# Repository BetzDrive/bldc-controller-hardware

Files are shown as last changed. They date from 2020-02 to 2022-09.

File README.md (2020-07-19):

# Betz Drive - A BLDC Controller

This board is designed for low-speed, high torque motor applications that require
highly precise positional and torque commands.

## Features

 * Chainable Initialization. Input/output connectors and 'disco-bus' pins provide
 dynamic initialization, allowing for easy replacement of any board (no hard coded ids).
 
 * High Precision Current Readings
 
 * 12-bit Precision Positional Readings [AS5047U-HTSM](https://ams.com/documents/20143/36005/AS5047U_DS000637_1-00.pdf)
 
 * Thermal Sensitivity
 
 * Optional 20-pin header with 9 GPIO pins, I2C, 3.3V rail, and ground for add-on functionality!
 
## Renderings

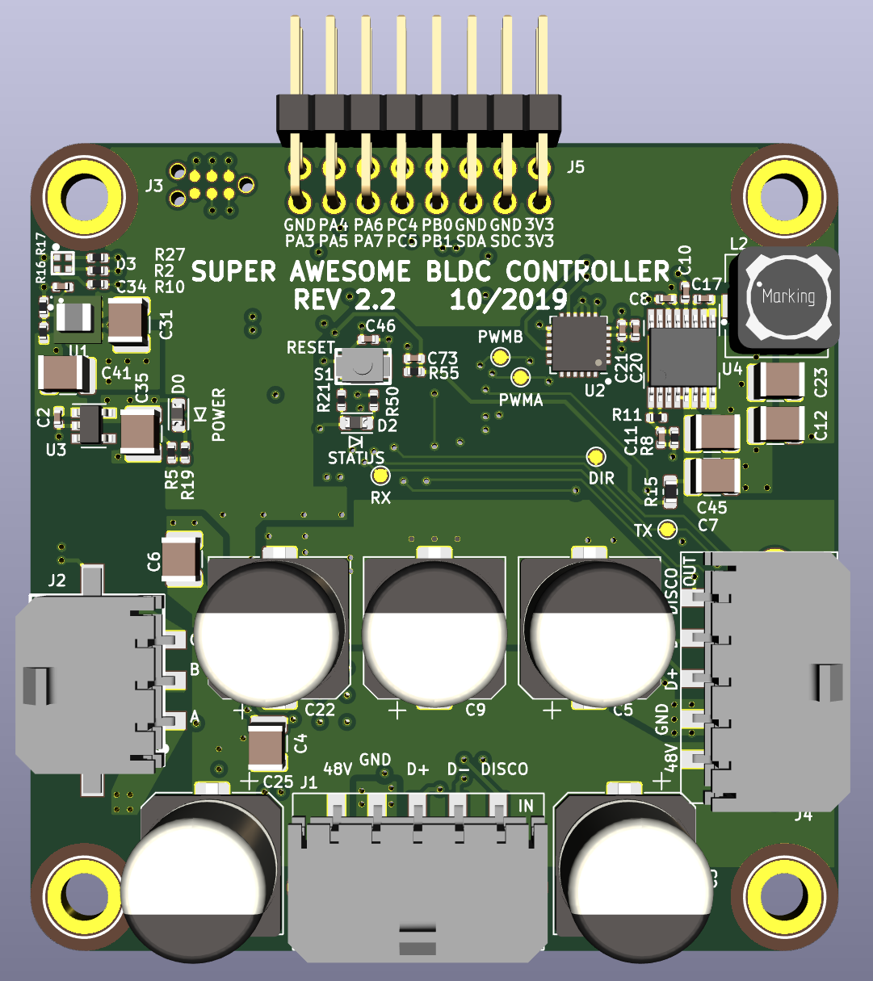
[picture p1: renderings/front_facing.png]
3D Front

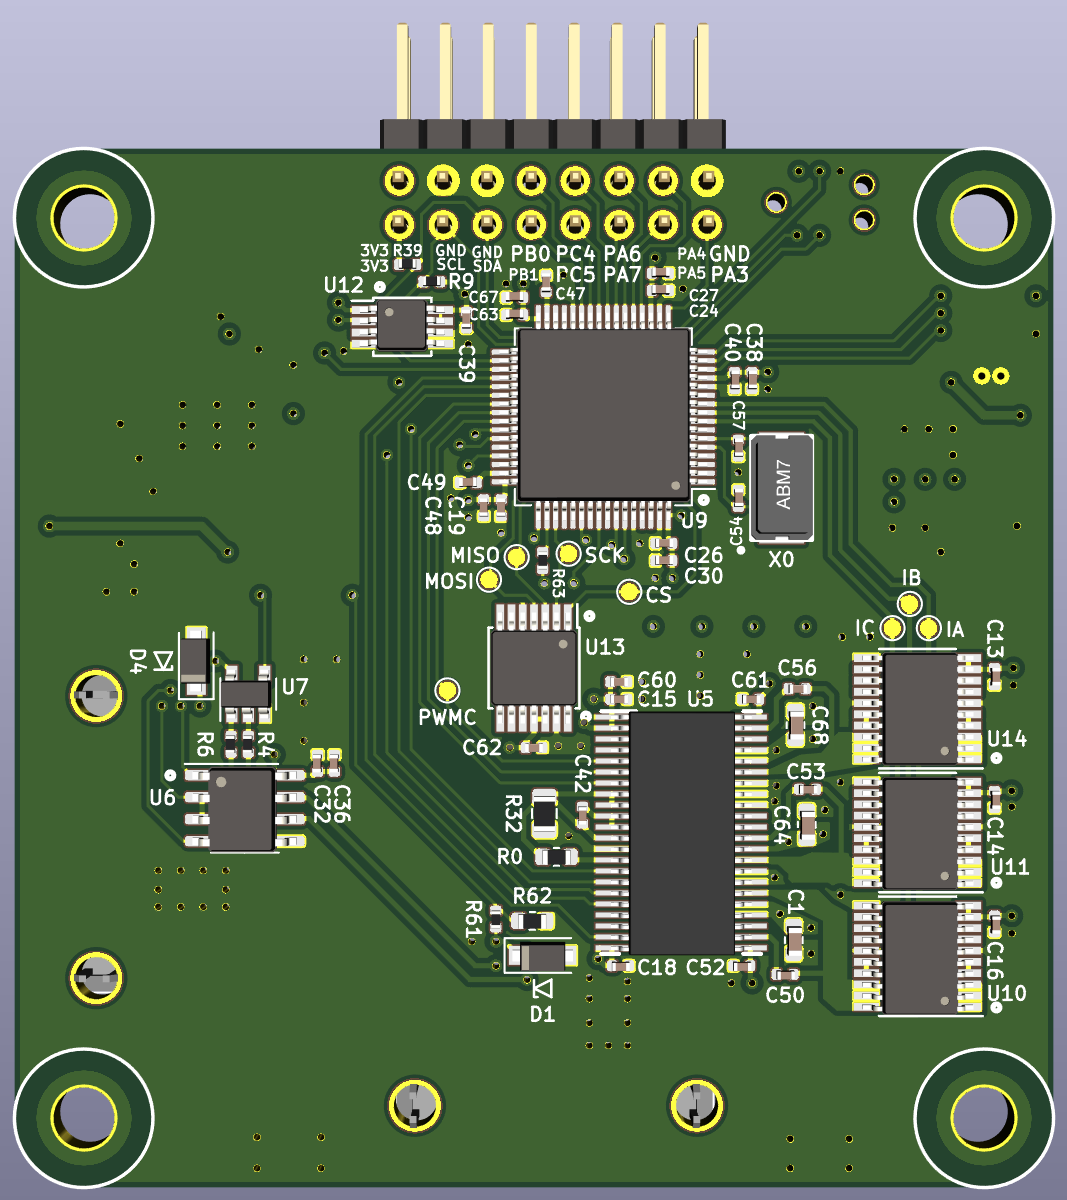
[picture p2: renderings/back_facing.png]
3D Back


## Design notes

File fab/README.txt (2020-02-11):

PCB fabrication notes
====
 * 4 layers
 * green soldermask, white silkscreen
 * rectangular, 60mm x 60mm
 * 1.6mm finished thickness
 * minimum via drill 15mil
 * minimum trace/space 7mil

Assembly notes:
====
 * double-sided SMT, heavy parts on top side
 * two connectors with through-hole mounting tabs
 * please ignore all parts with "Do Not Populate" (DNP) part numbers

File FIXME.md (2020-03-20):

 * bring an extra UART TX pin to a header for printf() debugging

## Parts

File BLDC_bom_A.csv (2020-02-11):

Component | Quantity Per PCB | References | Value | Footprint | Tolerance | MFN | MPN | D1N | D1PN | Maximum Voltage | Maximum Power
1 | 3 | C1 C64 C68 | 100n | C_0603_1608Metric | 10% | Samsung | CL10B104KC8NNNC | Digikey | 1276-6807-1-ND | 100.0V
2 | 19 | C13 C14 C16 C19 C21 C24 C26 C32 C39 C40 C42 C46 C50 C53 C56 C61 C62 C63 C73 | 100n | C_0402_1005Metric | 10% | Samsung | CL05A104KA5NNNC | Digikey | 1276-1043-1-ND | 25.0V
3 | 5 | C3 C5 C9 C22 C25 | 100u | CP_Elec_10x10 | 20% | Panasonic | EEE-1JA101P | Digikey | PCE3942CT-ND | 63.0V
4 | 2 | C54 C57 | 16p | C_0402_1005Metric | 5% | Murata | GJM1555C1H160GB01D | Digikey | 490-8081-1-ND | 50.0V
5 | 12 | C2 C15 C18 C20 C27 C30 C36 C38 C48 C52 C60 C67 | 1u | C_0402_1005Metric | 10% | Murata | GRM155R61E105KA12D | Digikey | 490-10017-1-ND | 25.0V
6 | 5 | C12 C23 C31 C35 C41 | 22u | C_1210_3225Metric | 10% | Samsung | CL32A226KAJNNNE | Digikey | 1276-1101-1-ND | 25V
7 | 4 | C8 C10 C47 C49 | 2u2 | C_0402_1005Metric | 10% | Murata | GRM155R61E225KE11D | Digikey | 490-12703-1-ND | 25.0V
8 | 1 | C17 | 470n | C_0402_1005Metric | 10% | Samsung | CL05A474KP5NNNC | Digikey | 1276-1173-1-ND | 10.0V
9 | 1 | C34 | 4n7 | C_0402_1005Metric | 10% | Yageo | CC0402KRX7R8BB472 | Digikey | 311-1039-1-ND | 25V
10 | 4 | C4 C6 C7 C45 | 4u7 | C_1210_3225Metric | 10% | TDK | C3225X7S2A475K200AB | Digikey | 445-6042-1-ND | 100V
11 | 1 | C11 | 82p | C_0402_1005Metric | 10% | AVX Corporation | 04025A820FAT2A | Digikey | 478-10115-1-ND | 50V
12 | 2 | D0 D2 | LTST-C190GKT | D_0603_1608Metric |  | Lite-On | LTST-C190GKT | Digikey | 160-1183-1-ND
13 | 2 | D1 D4 | SMF3.3 | D_SOD-123F |  | Littelfuse | SMF3.3 | Digikey | F7701CT-ND
14 | 1 | D3 | SMLP34RGB | rhom-SMLP34RGB-fp |  | Rohm | SMLP34RGB2W3 | Digikey | SMLP34RGB2W3CT-ND
15 | 2 | J1 J4 | 43650-0510 | molex-436500511 |  | Molex | 436500510 | Digikey | WM1888CT-ND
16 | 1 | J2 | 436500313 | molex-microfit-3-pkg |  | Molex | 436500313 | Digikey | WM1896CT-ND
17 | 1 | J5 | BONUS | PinHeader_2x08_P2.54mm_Horizontal |  | DNP | DNP | DNP | DNP
18 | 1 (DNF) | J3 | DNP | TC2030-MCP-NL-pkg |  | DNP | DNP | DNP | DNP
19 | 1 | L2 | 100u | L_7.3x7.3_H4.5 | 20% | Wurth | 744777920 | Digikey | 732-1199
20 | 6 | R2 R5 R10 R19 R27 R50 | 150R | R_0402_1005Metric | 1% | Panasonic | ERJ-2RKF1500X | Digikey | P150LCT-ND |  | 0.0625W
21 | 1 | R17 | 180k | R_0402_1005Metric | 1% | Yageo | RC0402FR-07180KL | Digikey | 311-180KLRCT-ND |  | 0.0625W
22 | 1 | R8 | 1M | R_0402_1005Metric | 1% | Yageo | RC0402FR-071ML | Digikey | 311-1.00MLRCT-ND |  | 0.0625W
23 | 1 | R32 | 1R | R_0805_2012Metric | 1% | Panasonic | ERJ-6DQF1R0V | Digikey | P19268CT-ND |  | 0.333W
24 | 6 | R9 R21 R39 R55 R61 R63 | 2k21 | R_0402_1005Metric | 1% | Panasonic | ERJ-2RKF2211X | Digikey | P2.21KLCT-ND |  | 0.0625W
25 | 3 | R0 R15 R62 | 49k9 | R_0603_1608Metric | 1% | Panasonic | ERJ-3EKF4992V | Digikey | P49.9KHCT-ND |  | 0.0625W
26 | 2 | R4 R6 | 56R2 | R_0402_1005Metric | 1% | Yageo | RC0402FR-0756R2L | Digikey | 311-56.2LRCT-ND |  | 0.0625W
27 | 1 | R16 | 681k | R_0402_1005Metric | 1% | Yageo | RC0402FR-07681KL | Digikey | YAG3212CT-ND |  | 0.0625W
28 | 1 | R11 | 91k | R_0402_1005Metric | 1% | Yageo | RC0402FR-0791KL | Digikey | 311-91.0KLRCT-ND |  | 0.0625W
29 | 1 | S1 | B3U-1000P | SW_B3U-1000P |  | Omron | B3U-1000P | Digikey | SW1020CT-ND
30 | 1 | U13 | AS5047U | TSSOP-14_4.4x5mm_P0.65mm |  | AMS | AS5047U-HTSM | Mouser | 985-AS5047U-HTSM
31 | 1 | U5 | DRV8312 | HTSSOP-44 |  | TI | DRV8312DDWR | Digikey | 296-29649-1-ND
32 | 1 | U2 | IIS328DQ | QFN-24-1EP_4x4mm_P0.5mm_EP2.6x2.6mm |  | ST | IIS328DQTR | Digikey | 497-15701-1-ND
33 | 3 | U10 U11 U14 | INA253 | TSSOP-20_4.4x6.5mm_P0.65mm |  | TI | INA253A2IPW | Digikey | 296-53071-ND
34 | 1 | U6 | ISL32458E | SOIC-8_3.9x4.9mm_P1.27mm |  | Renesas | ISL32458EIBZ-T7A | Digikey | ISL32458EIBZ-T7ACT-ND
35 | 1 | U4 | LM46000 | PWP0016G |  | TI | LM46000PWPR | Digikey | 296-40222-1-ND
36 | 1 | U1 | LMZ21700SIL | SIL0008E |  | TI | LMZ21700SILR | Digikey | 296-44325-1-ND
37 | 1 | U12 | MCP9808 | MSOP-8_3x3mm_P0.65mm |  | Microchip | MCP9808T-E/MS | Digikey | MCP9808T-E/MSCT-ND
38 | 1 | U7 | SN74LVC1G66DBV | SOT-23-5 |  | TI | SN74LVC1G66DBV | Digikey | 296-13253-1-ND
39 | 1 | U9 | STM32F405RG | LQFP-64_10x10mm_P0.5mm |  | ST | STM32F405RGT6 | Digikey | 497-11767-ND
40 | 1 | U3 | TLV702 | SOT-23-5 |  | TI | TLV70233DBVR | Digikey | 296-32415-1-ND
41 | 1 | X0 | ABM7-8.000MHZ-D2Y-T | ABM7-8MHZ-D2Y-T-pkg |  | Abracon LLC | ABM7-8.000MHZ-D2Y-T | Digikey | 535-9831-1-ND
Component Groups: | 41
Component Count: | 105
Fitted Components: | 104
Number of PCBs: | 1
Total components: | 104
Schematic Version: | A
Schematic Date: | 2019-08-22
PCB Variant: | ['default']
BoM Date: | Mon Oct 14 13:54:15 2019
Schematic Source: | /home/mquigley/hw/bldc-controller-hardware/BLDC.sch
KiCad Version: | Eeschema 5.99.0-unknown-e291576~100~ubuntu18.04.1

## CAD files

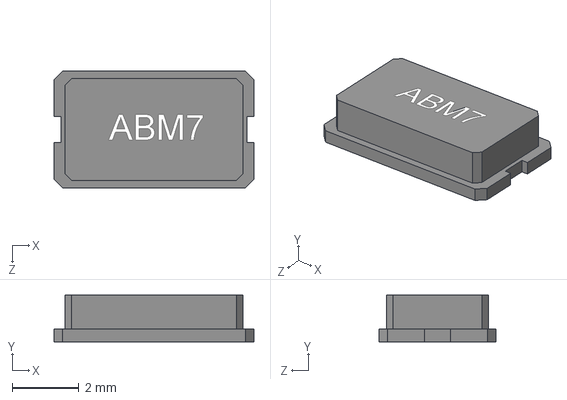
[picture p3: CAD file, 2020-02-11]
3d_models/ABM7.STEP
5.99 x 1.40 x 3.51 mm

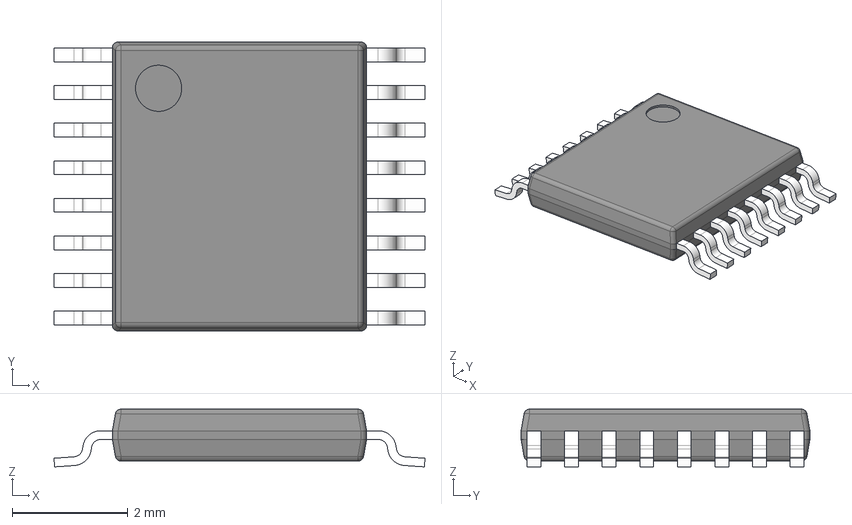
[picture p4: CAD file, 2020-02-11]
3d_models/PWP0016G.stp
6.42 x 5.00 x 1.00 mm
BODY-SO
LEAD-SO x 16
THERMALPAD-SO

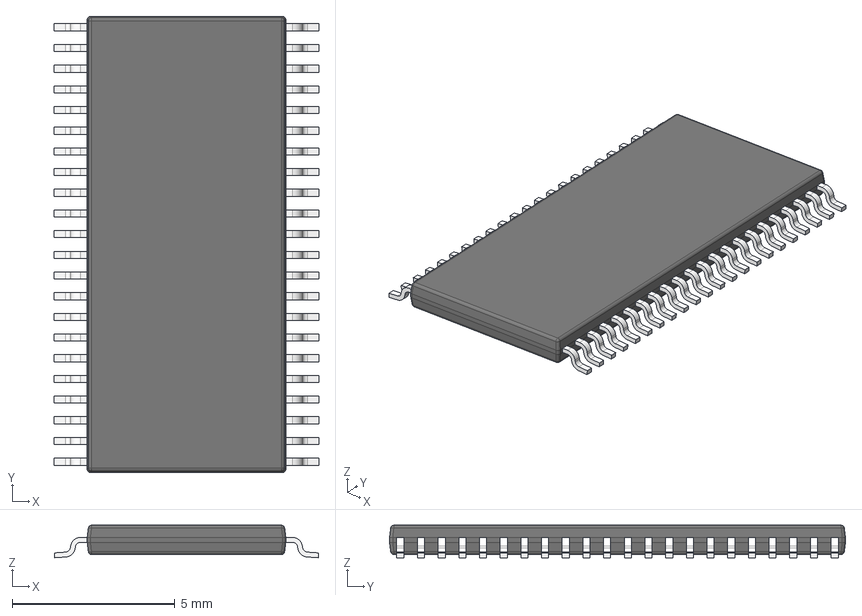
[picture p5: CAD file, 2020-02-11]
3d_models/DRV8312.stp
8.12 x 14.0 x 1.00 mm
BODY-SO
LEAD-SO x 44
THERMALPAD-SO
PIN1-ID

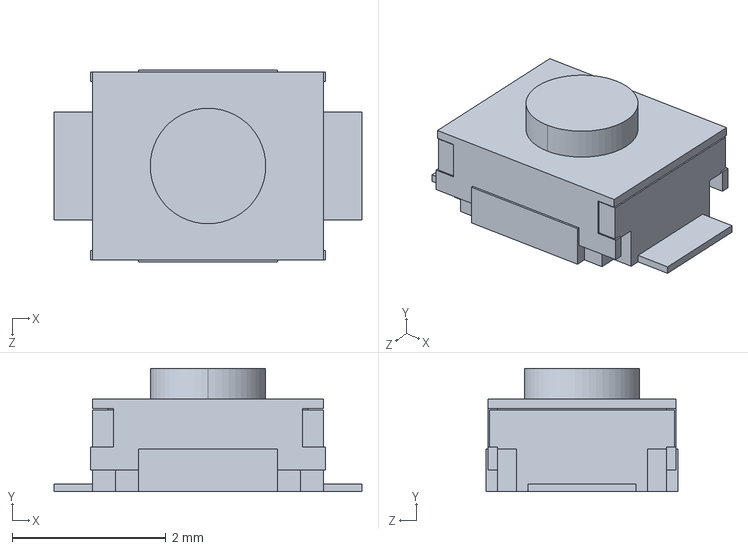
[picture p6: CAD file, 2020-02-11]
3d_models/B3U_1000P.step
4.00 x 1.60 x 2.50 mm

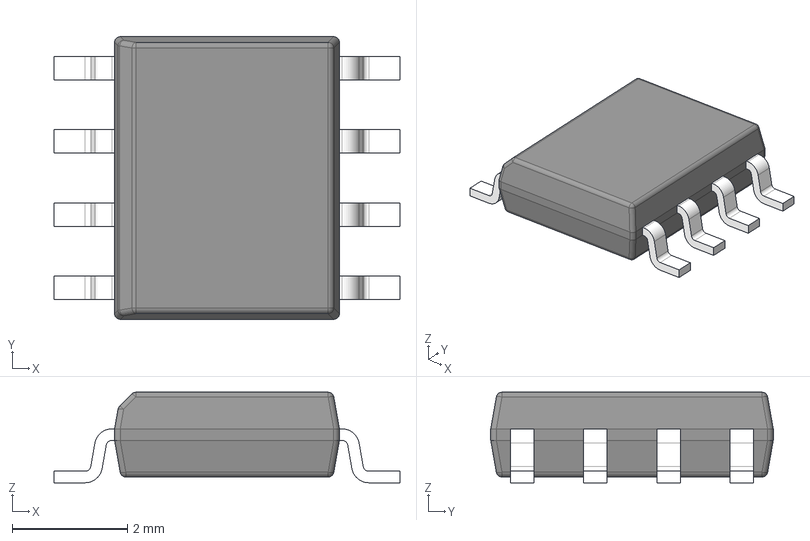
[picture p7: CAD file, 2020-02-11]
3d_models/LM5163.stp
6.00 x 4.90 x 1.57 mm
BODY-SO
LEAD-SO x 8
THERMALPAD-SO

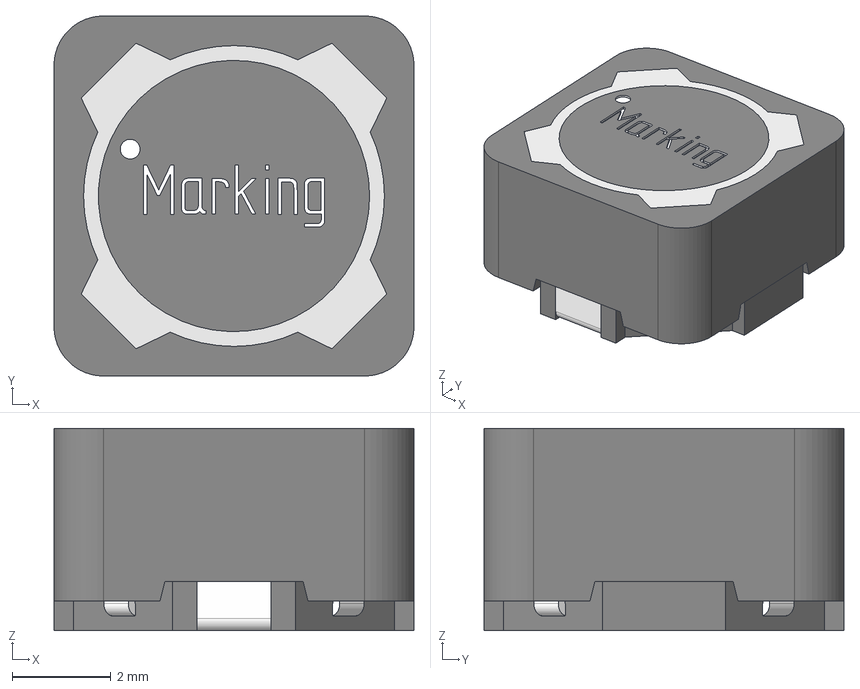
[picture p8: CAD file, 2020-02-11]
3d_models/STEP-WE-PD-7345-Plastic-rev1.stp
7.30 x 7.30 x 4.10 mm
Boden
Pins
Kern
Schirmring
Kleber

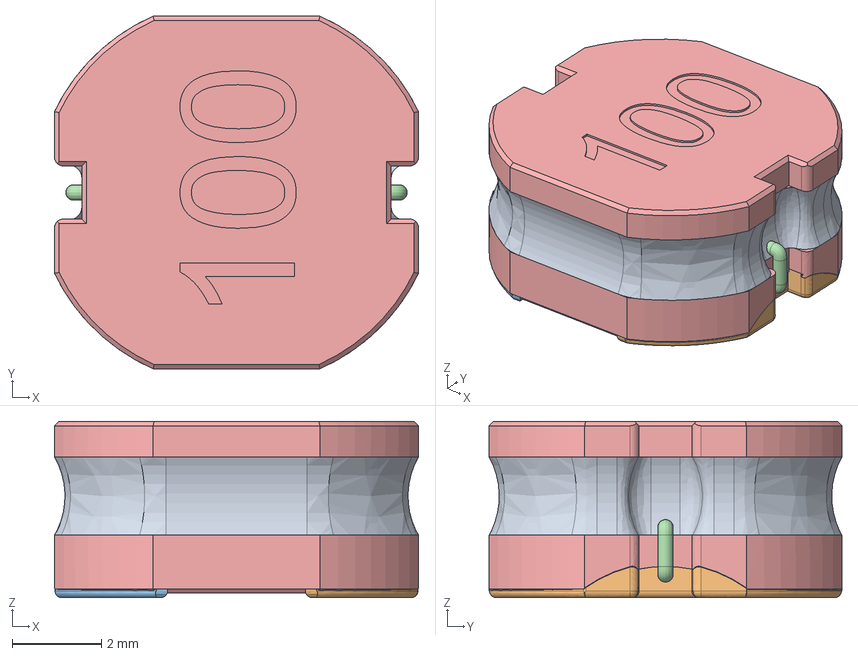
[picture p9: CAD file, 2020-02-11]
3d_models/srn8040.stp
8.15 x 7.90 x 3.95 mm

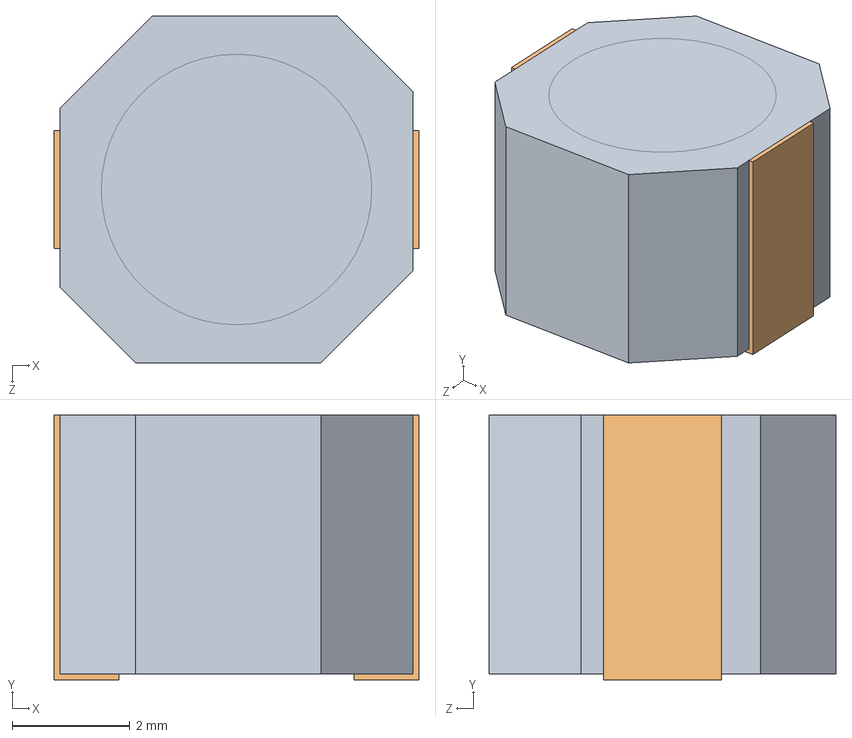
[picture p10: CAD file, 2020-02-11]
3d_models/clf6045.step
6.20 x 4.50 x 5.90 mm
CLF6045素体
CLF6045端子 x 2

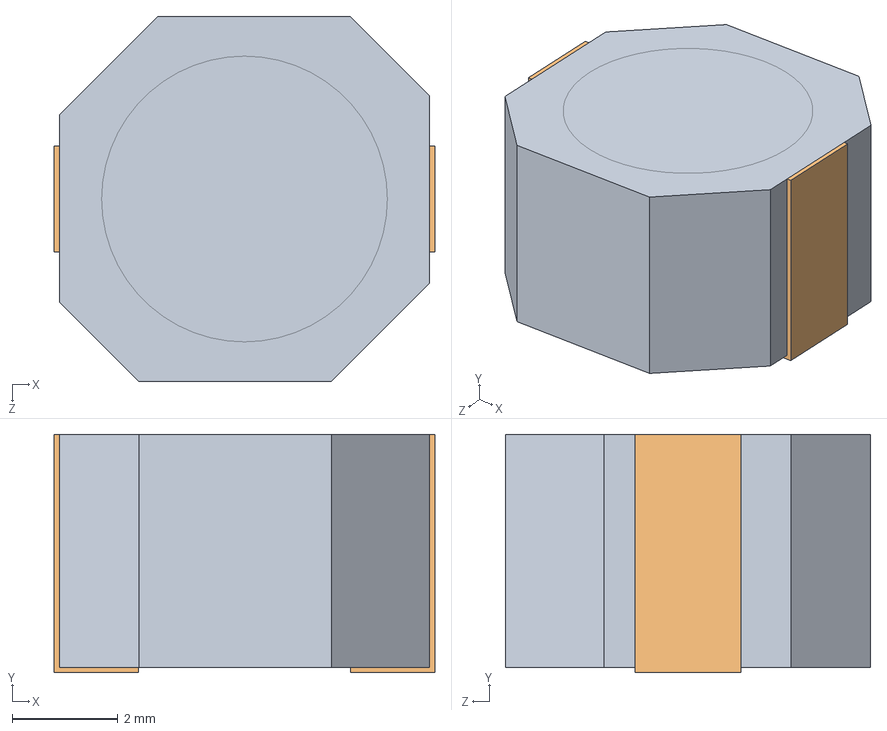
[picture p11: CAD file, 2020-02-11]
3d_models/clf7045.step
7.20 x 4.50 x 6.90 mm
CLF7045素体
CLF7045端子 x 2

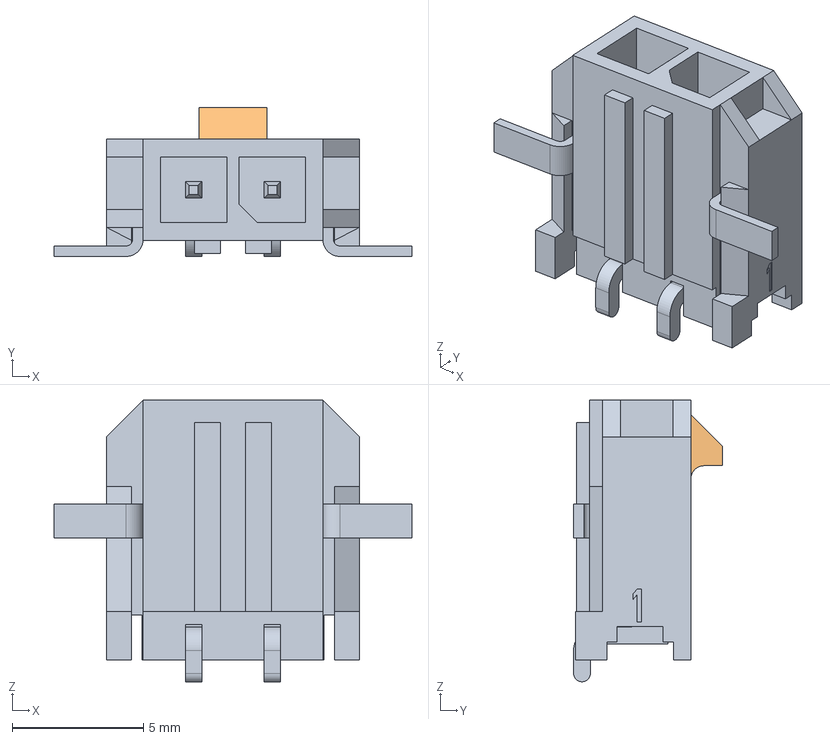
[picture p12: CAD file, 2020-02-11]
3d_models/436500213.stp
13.7 x 5.67 x 10.7 mm

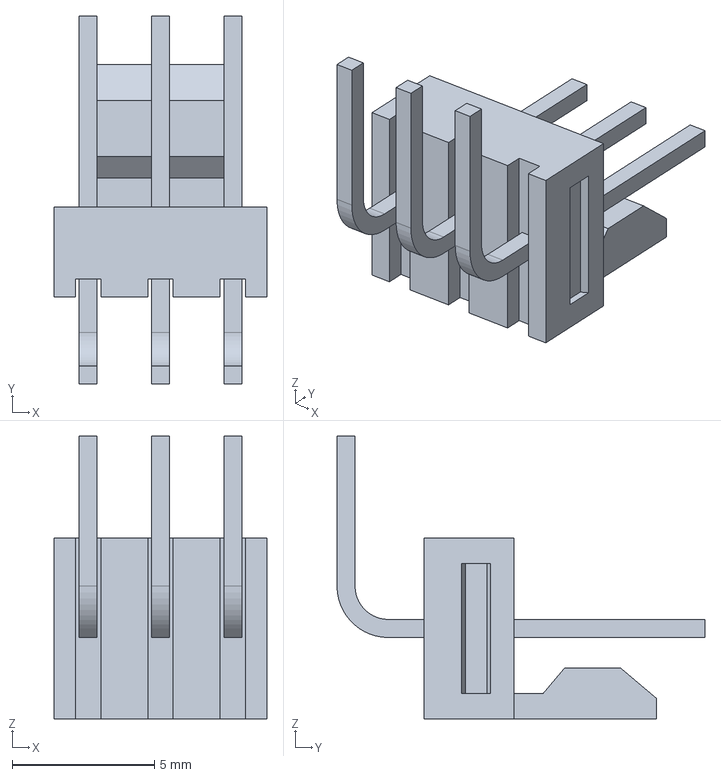
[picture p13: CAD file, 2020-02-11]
3d_models/022053031.stp
7.47 x 12.9 x 9.93 mm

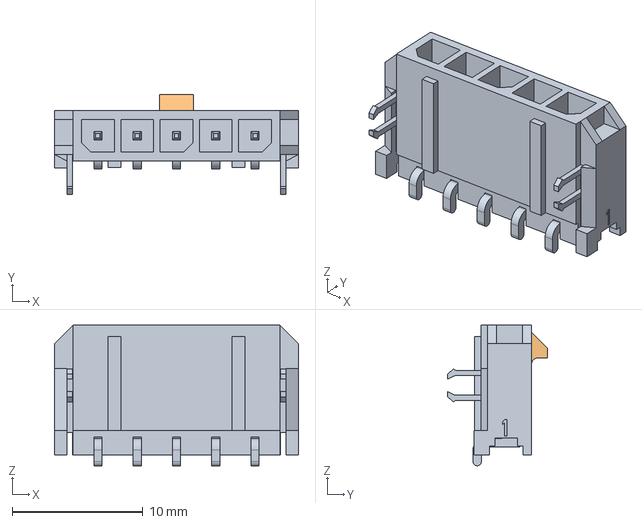
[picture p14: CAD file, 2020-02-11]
3d_models/436500511.stp
18.6 x 7.60 x 10.7 mm

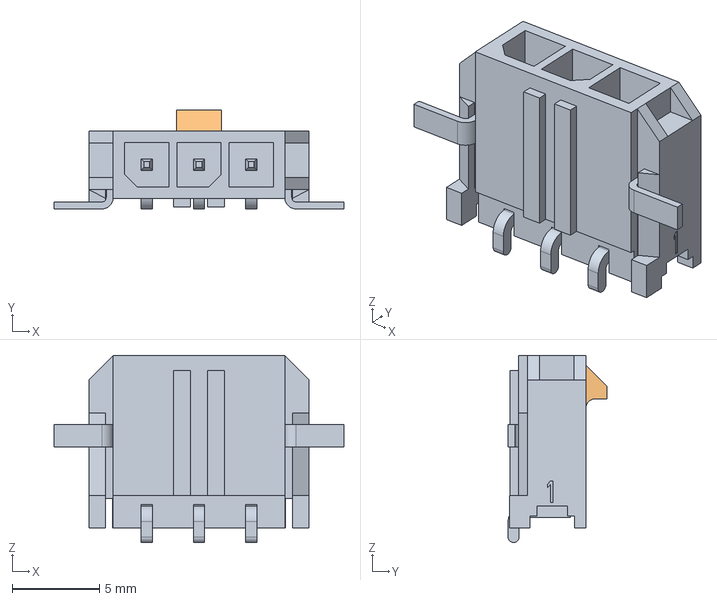
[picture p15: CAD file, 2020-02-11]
3d_models/436500313.stp
16.6 x 5.67 x 10.7 mm

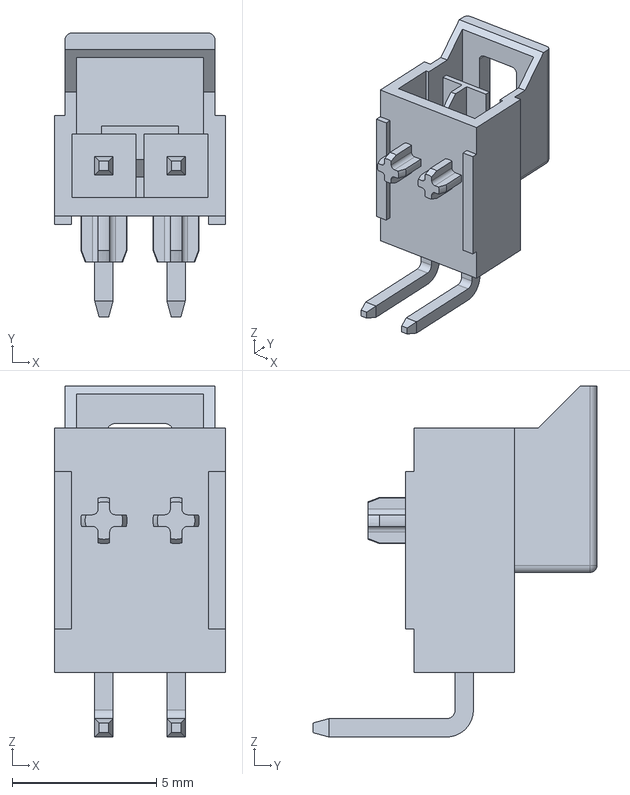
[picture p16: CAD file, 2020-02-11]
3d_models/1053131202.stp
5.94 x 9.84 x 12.2 mm

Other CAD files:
3d_models/436500513.stp
3d_models/LMZ21701.stp

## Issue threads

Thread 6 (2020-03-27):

README is missing

AlexDaniel, 2020-03-27:
I think this project is missing a helpful README file with pictures and stuff.

By the way, is there any info available about the betz project itself? What's the goal? How does it compare to ODrive?

gbalke, 2020-04-18:
Apologies for the delay. We're in a bit of a mix due to the current situation (difficult to access our workspace). We'll be putting together a summary of the drives and a comparison as soon as possible!

gbalke, 2021-03-01:
@AlexDaniel looks like this got lost to the ether haha. By now I'm guessing you've picked up a controller for whatever application you were working on. I'm only just now getting some time to focus on the project again. Is there a specific use case you had in mind? I think it'd help to know if there's more information you'd like to gleam other than what I've written on [betzdrive.com](betzdrive.com).

AlexDaniel, 2021-03-01:
It's OK, I often get notifications from tickets that I reported many years ago :)

Meanwhile I stumbled upon https://docs.simplefoc.com/ and got a compatible board (they are cheap and widely available). Still didn't get to truly use it in a project yet because I got carried away with other things, but eventually I'll get back to it.

gbalke, 2021-03-01:
Oh that looks pretty cool! :+1:

The main motivator for this BLDC was to have an all-in-one where the encoder, thermal sensor, and IMU were co-located. Having all of these be independent systems adds to assembly complexity and additional wiring complications. I think the link I added to [Blue](https://www.berkeleyopenarms.org/) will help people understand the reasoning behind this design.

I'll close up this ticket with the hope that enough information is covered on the website :smile:.

Closed 2021-03-01.

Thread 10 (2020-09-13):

Inrush Current at 3.3V Large

gbalke, 2020-09-13:
When testing the interface board for slow-start, I observed that inrush current at 3.3V was very high for the motor controller boards. This led to numerous I-max bumps and over-current timeout increases to account for 8 boards in series being used by the Blue project. The goal for this issue is to shift this low-voltage current draw into a higher voltage range such that the supply-side sees a much smaller spike. As of PR #8, this has been shifted up to 12V. This issue will track the success of that change and the specifics of the problem.

Note that these scope images are taken with a really cheap car current probe, hence the noise.

These first two images are the only ones with the proper current settings (was learning how to use this setting on my scope). Both are done with 8 motor controllers.
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
Note the smooth current draw after start-up, this is the charging current draw expected. The second bump is the large current draw of the 8 boards starting up around 3.3V. This is one of the better captures to see this issue. In this case, the current spike caused the controller to shut down the supply.
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
10x these current readings (five boards)
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
(100mV = 1A) Three boards:
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
Two boards:
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
One Board:
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

gbalke, 2021-03-01:
This was caused by the 8x motor controllers starting up at 3.3V and the MCUs + peripherals pulling a large amount of current. This was handled in #8 as it is not the responsibility of the interface board to handle this spike (spike is now shifted to 12-16V ish which pulls the same power at a much lower current).

Closed 2021-03-01.

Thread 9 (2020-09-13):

Significantly reduced communication reliability between v2.0 and v2.2

gbalke, 2020-09-13:
When running some communication frequency tests, I observed unusually high communication error rates with [v2.2](https://github.com/BetzDrive/bldc-controller-hardware/tree/v2.2) boards. I thought this was just a fluke but I decided to swap out for a [v2.0](https://github.com/BetzDrive/bldc-controller-hardware/tree/v2.0) board to see if the same issues would exist. To my surprise, the v2.0 board had far superior performance.

The setup I used (note I hot plugged the 5 pin output which broke the RS485 conversion circuitry on this interface board, it worked just fine prior to that):
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

Here are the results of each board while running a [1000 packet frequency test](https://github.com/berkeleyopenarms/blue_core/pull/98):
```
v2.0
[ INFO] [1600023829.823944194]: comm time dt: 0.001020, freq: 980.789576, error rate: 0.00%
[ INFO] [1600023830.885020693]: comm time dt: 0.001061, freq: 942.431438, error rate: 0.00%
[ INFO] [1600023831.949970126]: comm time dt: 0.001065, freq: 939.006689, error rate: 0.00%
[ INFO] [1600023833.017809807]: comm time dt: 0.001068, freq: 936.479761, error rate: 0.00%
[ INFO] [1600023834.207183691]: comm time dt: 0.001189, freq: 840.779238, error rate: 0.00%
[ INFO] [1600023835.278650344]: comm time dt: 0.001071, freq: 933.292096, error rate: 0.00%
[ INFO] [1600023836.526089476]: comm time dt: 0.001247, freq: 801.641464, error rate: 0.10%
[ INFO] [1600023837.562513888]: comm time dt: 0.001036, freq: 964.855147, error rate: 0.10%
[ INFO] [1600023838.660987897]: comm time dt: 0.001098, freq: 910.355054, error rate: 0.00%
[ INFO] [1600023839.769512690]: comm time dt: 0.001109, freq: 902.098902, error rate: 0.00%
[ INFO] [1600023840.896899233]: comm time dt: 0.001127, freq: 887.011400, error rate: 0.10%
[ INFO] [1600023841.988356426]: comm time dt: 0.001091, freq: 916.205157, error rate: 0.10%
[ INFO] [1600023843.113874297]: comm time dt: 0.001126, freq: 888.479058, error rate: 0.00%
[ INFO] [1600023844.206556070]: comm time dt: 0.001093, freq: 915.178266, error rate: 0.00%
```
```
v2.2
[ INFO] [1600023744.000228761]: comm time dt: 0.001210, freq: 826.165763, error rate: 1.00%
[ INFO] [1600023745.120665772]: comm time dt: 0.001120, freq: 892.501351, error rate: 0.50%
[ INFO] [1600023746.273147391]: comm time dt: 0.001152, freq: 867.689618, error rate: 1.10%
[ INFO] [1600023747.410961965]: comm time dt: 0.001138, freq: 878.880324, error rate: 0.50%
[ INFO] [1600023748.614074245]: comm time dt: 0.001203, freq: 831.176878, error rate: 1.20%
[ INFO] [1600023749.759499979]: comm time dt: 0.001145, freq: 873.039530, error rate: 0.60%
[ INFO] [1600023750.959934337]: comm time dt: 0.001200, freq: 833.032582, error rate: 0.50%
[ INFO] [1600023752.165648419]: comm time dt: 0.001206, freq: 829.379070, error rate: 1.20%
[ INFO] [1600023753.342919607]: comm time dt: 0.001177, freq: 849.433090, error rate: 1.00%
[ INFO] [1600023754.485081835]: comm time dt: 0.001142, freq: 875.524857, error rate: 0.50%
[ INFO] [1600023755.651654054]: comm time dt: 0.001167, freq: 857.213028, error rate: 0.80%
[ INFO] [1600023756.850065793]: comm time dt: 0.001198, freq: 834.437304, error rate: 1.50%
[ INFO] [1600023757.963656416]: comm time dt: 0.001114, freq: 897.995186, error rate: 0.80%
[ INFO] [1600023759.199031016]: comm time dt: 0.001235, freq: 809.472216, error rate: 1.10%
```

I reviewed both schematics and noticed that the circuits are identical

v2.2:
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

v2.0:
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

This leaves me thinking that the only issue could arise from a discrepancy in layout. When I browsed the layout, I noticed that, if anything, the v2.2 boards have a path that is more ideal than the v2.0 boards (much less distance and vias between the RS485 chip and the connector). Because of this, I looked more generally at the board design. I noticed that in v2.0, the majority of the pours are for GND. This is not the case for v2.2 where In1 is primarily 3.3v, In2 is GND, Back is GND, and Front is a mixture of 48V and GND over the sections through which comms travels. My main concern here is interference as I know signals can be finicky. Another idea is that the RS485 chip was moved closer to the connectors (which means RS485 will be better off) but the on-board UART now has further to travel, and, consequently, suffers more from the on-board noise. This may be a bad trade-off as RS485 is a much more robust signal.

I've attached some oscilloscope readings to show what a missed response looks like when talking with two boards (using the math operation to show the differential pair). Two boards are used as the error rate increases (N^2) with the number of boards, making it easier to catch these on the scope. The error rate when using two boards is about 4+-2%. While obviously not precise enough to determine signal integrity, this is mostly meant to show the observed behavior in the interest of reproducing the issue. The close-ups that I viewed have sharp signal edges (to be expected, this is only ~1MHz).

This is a normal, successful transmission.
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

Based on the [protocol](https://github.com/BetzDrive/bldc-controller/blob/master/docs/protocol_v3.md), one communication error occurs when either the second board misses the host message or misses the reply of the first board.
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

If the first board misses the host message, regardless of what happens down-stream, no boards will respond. This is due to a counter on each board which is set by the board's message index in the host packet. When a board observes a reply from any board, it decrements this counter. When its counter reaches zero (or 1 I can't remember), it sends its reply!
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

Any help on identifying what could be the problem would be greatly appreciated! I'll require that this be the primary driver of the v2.3 release.

Edit: Note that both the v2.0 and v2.2 boards I used in testing are from the same manufacturer. The same errors are found in another batch of v2.2 boards from a different manufacturer.

Edit 2: Here's some printouts of the schematics.
[v2.0 schematic](https://github.com/BetzDrive/bldc-controller-hardware/files/5215538/v2_0_spec.pdf)
[v2.2 schematic](https://github.com/BetzDrive/bldc-controller-hardware/files/5215539/v2_2_spec.pdf)

gbalke, 2020-09-13:
@codebot @luca-della-vedova any thoughts?

gbalke, 2020-09-14:
I removed U6 and terminated the RS485 directly by connecting A and B. Does not seem to have improved error rates:
```
[ INFO] [1600044100.806813912]: comm time dt: 0.001232, freq: 811.909066, error rate: 1.00%
[ INFO] [1600044101.984372867]: comm time dt: 0.001178, freq: 849.200731, error rate: 0.70%
[ INFO] [1600044103.207265780]: comm time dt: 0.001223, freq: 817.740651, error rate: 0.60%
[ INFO] [1600044104.280283827]: comm time dt: 0.001073, freq: 931.944490, error rate: 0.50%
[ INFO] [1600044105.442910183]: comm time dt: 0.001163, freq: 860.123145, error rate: 1.20%
[ INFO] [1600044106.644414673]: comm time dt: 0.001202, freq: 832.290339, error rate: 0.80%
[ INFO] [1600044107.799858538]: comm time dt: 0.001155, freq: 865.461834, error rate: 1.20%
[ INFO] [1600044109.011259536]: comm time dt: 0.001211, freq: 825.497812, error rate: 1.60%
```

codebot, 2020-09-14:
Can you also post scope traces of the RS485 lines (A and B), in addition to the subtract operator? It seems odd that the motor-board RS485 is showing half the amplitude of the interface board.

Single-ended UART signal integrity shouldn't be an issue across a small PCB, regardless of reference plane (GND vs 3v3, etc). It's still low-frequency, only a few MHz.

Can you also probe the UART lines on the motor board? I'm wondering if a trailing "blip" gets triggered in the UART after the STOP pulse. I saw that earlier on my interface boards, but adding a bias network to the interface board RS485 lines (pulling A one direction, pulling B one direction) fixed it. It looks like the interface board in the photo doesn't have this mod; it requires a SMT resistor straddling U4 and another sneaking between two pins of U3. Do you have an interface board with those resistors added to test out?

gbalke, 2020-09-14:
I don't have that mod on my interface board although I've bypassed the FTDI. I can attempt to create some form of biasing using ground and 5V on my dongle board. I'm not sure if this fully explains the issue though as I'd imagine that's something that would effect both controllers equally...

Here's a scope of RS485 with both channels included with the math operation. I agree that it's strange to see them reading only half amplitude... This doesn't explain why they would miss the host packet in the first place though (which is shown to happen above).

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

codebot, 2020-09-14:
Ahh ok, this is starting to make sense. I believe that without the bias-resistor mod on the interface board, "sometimes" you get a super-fast blip at the end of a transmission. If you probe the UART RX line on a motor board (TP9), I think you'll see it "sometimes." In my testing, this "sometimes" causes a reception of an 0x00 or 0xff byte, which puts the packet parser in a weird state and makes it miss the next packet. Because it's a marginal thing, it doesn't happen all the time, and due to IC process variation, it affects some chips more than others. To provide some margin, we need the bias resistors on the interface board to pull the RS485 lines to a defined state when nobody is transmitting. This was my bad. It's the second bullet in the FIXME for the `interface-board` repo: https://github.com/BetzDrive/interface-board/blob/master/hardware/FIXME

I'll send a photo of the board mod required to do this. It's a bit tricky, but not totally crazy.

codebot, 2020-09-14:
Two 486-ohm 0603 resistors are added in the photo below. The one between C24 and U4 is straightforward. The one on top of U4 is more tricky, but with a few solder blobs and some patience, it's not too bad. The goal of these resistors is to ensure that when nobody is driving the bus, the RS485 lines float apart enough to always ensure that A>B by enough margin to guarantee a "0" state to all RS485 receivers on the bus. The most important time for this is immediately after a transmitter stops transmitting, since the lines want to "bounce" a bit at that instant, which sometimes produces a trailing "blip" if these resistors aren't there to fight it.

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
gbalke, 2020-09-30:
After testing a set of V2.1 boards, I've confirmed that they are not experiencing this issue. I realize now that an issue with the hardware is rather unlikely and so I've instead turned my attention towards the firmware. Though minor, the budgeting of CPU allocation has, in the past effected communication rate. To test this, I commented out all threads save for the communication thread and observed almost no missed packets. With this in mind, I can focus on this as a firmware issue instead of a hardware issue.

gbalke, 2020-10-01:
I've found that commit https://github.com/BetzDrive/bldc-controller/pull/27/commits/18629af495c4920166dc24ebda9c619d19ce959e in https://github.com/BetzDrive/bldc-controller/pull/27 performs with very little to no errors. This confirms my suspicion that this is a firmware issue and I'll be closing this issue. I'll be debugging this on the firmware side and open a corresponding issue.

codebot, 2020-10-01:
Interesting. I'll be really interested to hear how it goes as you continue to zero in on the problem. So the v2.2 boards seem to be innocent of causing this problem?

gbalke, 2020-10-01:
> Interesting. I'll be really interested to hear how it goes as you continue to zero in on the problem. So the v2.2 boards seem to be innocent of causing this problem?

Yeah, it's really funky. Please refer to the issue I just created! I'll be poking at it throughout the week.

Closed 2020-10-01.

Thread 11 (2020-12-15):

BLDC.sch file missing?

JorgeMaker, 2020-12-15:
Hi, I'm trying to open your design with Kicad but it indicates that the BLDC.sch file is missing. Do you know how I can solve the problem?
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

gbalke, 2020-12-15:
Heya, we use the Kicad-nightly build for development. You'll have to be on the bleeding edge to view the files! I hope that's okay 🙂

JorgeMaker, 2020-12-15:
Thank you very much for your quick answer :) I will try Kicad-nightly build.

PS: Congrats for you amazing project.  I am trying to do something very similar but using CAN instead of RS485 and  SimpleFOClibrary and I am ver interesting in learning from your project

Closed 2020-12-15.

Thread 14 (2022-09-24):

[WIP] Connector Reliability

gbalke, 2022-09-24:
Very much a WIP/Brain dump. Feel free to comment.

After a lot of use, I've found molex microfits to hold up poorly to stress. I saw HEBI robotics using RJ45 and thought it might be a reasonable approach. I'm interested in brainstorming other possible connectors and seeing if there's something that will hold up to the use-case.

## Connector Requirements
* Cheap (hopefully < $3). That's the name of the game for this robot actuator.
* High Power. I think we can easily pull 8-10A on accident and I'd rather not melt the connector in this case. It is worth noting that 21 Gauge wire hasn't had any issues with the normal arm load so I think I'm drawing a lot less power through the arm than I expected.

## Microfit
### Benefits
* High current rating (8.5A)

### Issues
The crimps used for microfit are folded sheet metal.
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
As the robot moves around, the cables have a small amount of motion. This ends up wiggling the crimped wires and slowly opens up this folded box. Once it's spread open enough, reliable continuity goes out the window.

## RJ45
### Benefits
To my understanding, RJ45 offers a highly reliable connection interface. I believe this is the case because of the spring system in the pin engagement. This allows the connector to wiggle without losing connectivity. I found some in-plane connectors on digikey that will require some board re-design (as they will collide with the passives when stacked). But they have a shorter final height than the bulk caps which is a win!
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
The less optimal part is that there will be big board cut-outs.
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

The other big plus of RJ45 is that ethernet cables are dirt cheap. If we can just use cables off the shelf that would be awesome (however using any old cable will definitely not work).

### Issues
* The main concern I have overall with this method is current limits in the wiring and connectors. The connector referenced above has a 1.5A limit per pin. I was planning to use 2 pairs for power rails but that still only gives us 3A.
* Cable flexibility is another big concern. In order to get enough power through the wires, I think 23 gauge wire is necessary. I saw a lot of potential sellers for this but it was always solid core wire instead of stranded. I ended up getting some just to fiddle with and found it waaaay too stiff to use in practice.

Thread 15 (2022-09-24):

[WIP] Hardware Upgrades

gbalke, 2022-09-24:
Given the age of the parts, I definitely believe the performance of the motor controller can be improved at a lower cost. I'm going to do a quick breakdown of current components and specs and update this issue with alternatives.

Based on current firmware size and bootloader size, I think it's possible to get away with a much smaller FLASH section.
```
 text    data     bss     dec     hex filename                         
17589    1532    5288   24409    5f59 bazel-build/bin/bootloader/bootloader.elf

 text    data     bss     dec     hex filename                     
52413    1620   75180  129213   1f8bd bazel-build/bin/firmware/firmware.elf
```
Note that bss is just static initialized RAM and does not count towards flash space.

### Microcontroller
* [STM32F405RGT6](https://www.digikey.com/en/products/detail/stmicroelectronics/STM32F405RGT6/2754208) ($15.84 & current micro)
  * RAM:   196kB (though the ld file only uses the first 112kB)
  * FLASH: 1MB
  * CLOCK: 168MHz
  * Package: 64LQFP (10x10mm)
* [STM32G431CBT6](https://www.digikey.com/en/products/detail/stmicroelectronics/STM32G431CBT6/10231567) ($8.01)
  * RAM:   32kB (I have some large buffers in the BSS that I can probably pull out to make this work)
  * FLASH: 128kB
  * CLOCK: 170MHz
  * Package: 48LQFP (7x7mm)
  * I think more RAM probably...

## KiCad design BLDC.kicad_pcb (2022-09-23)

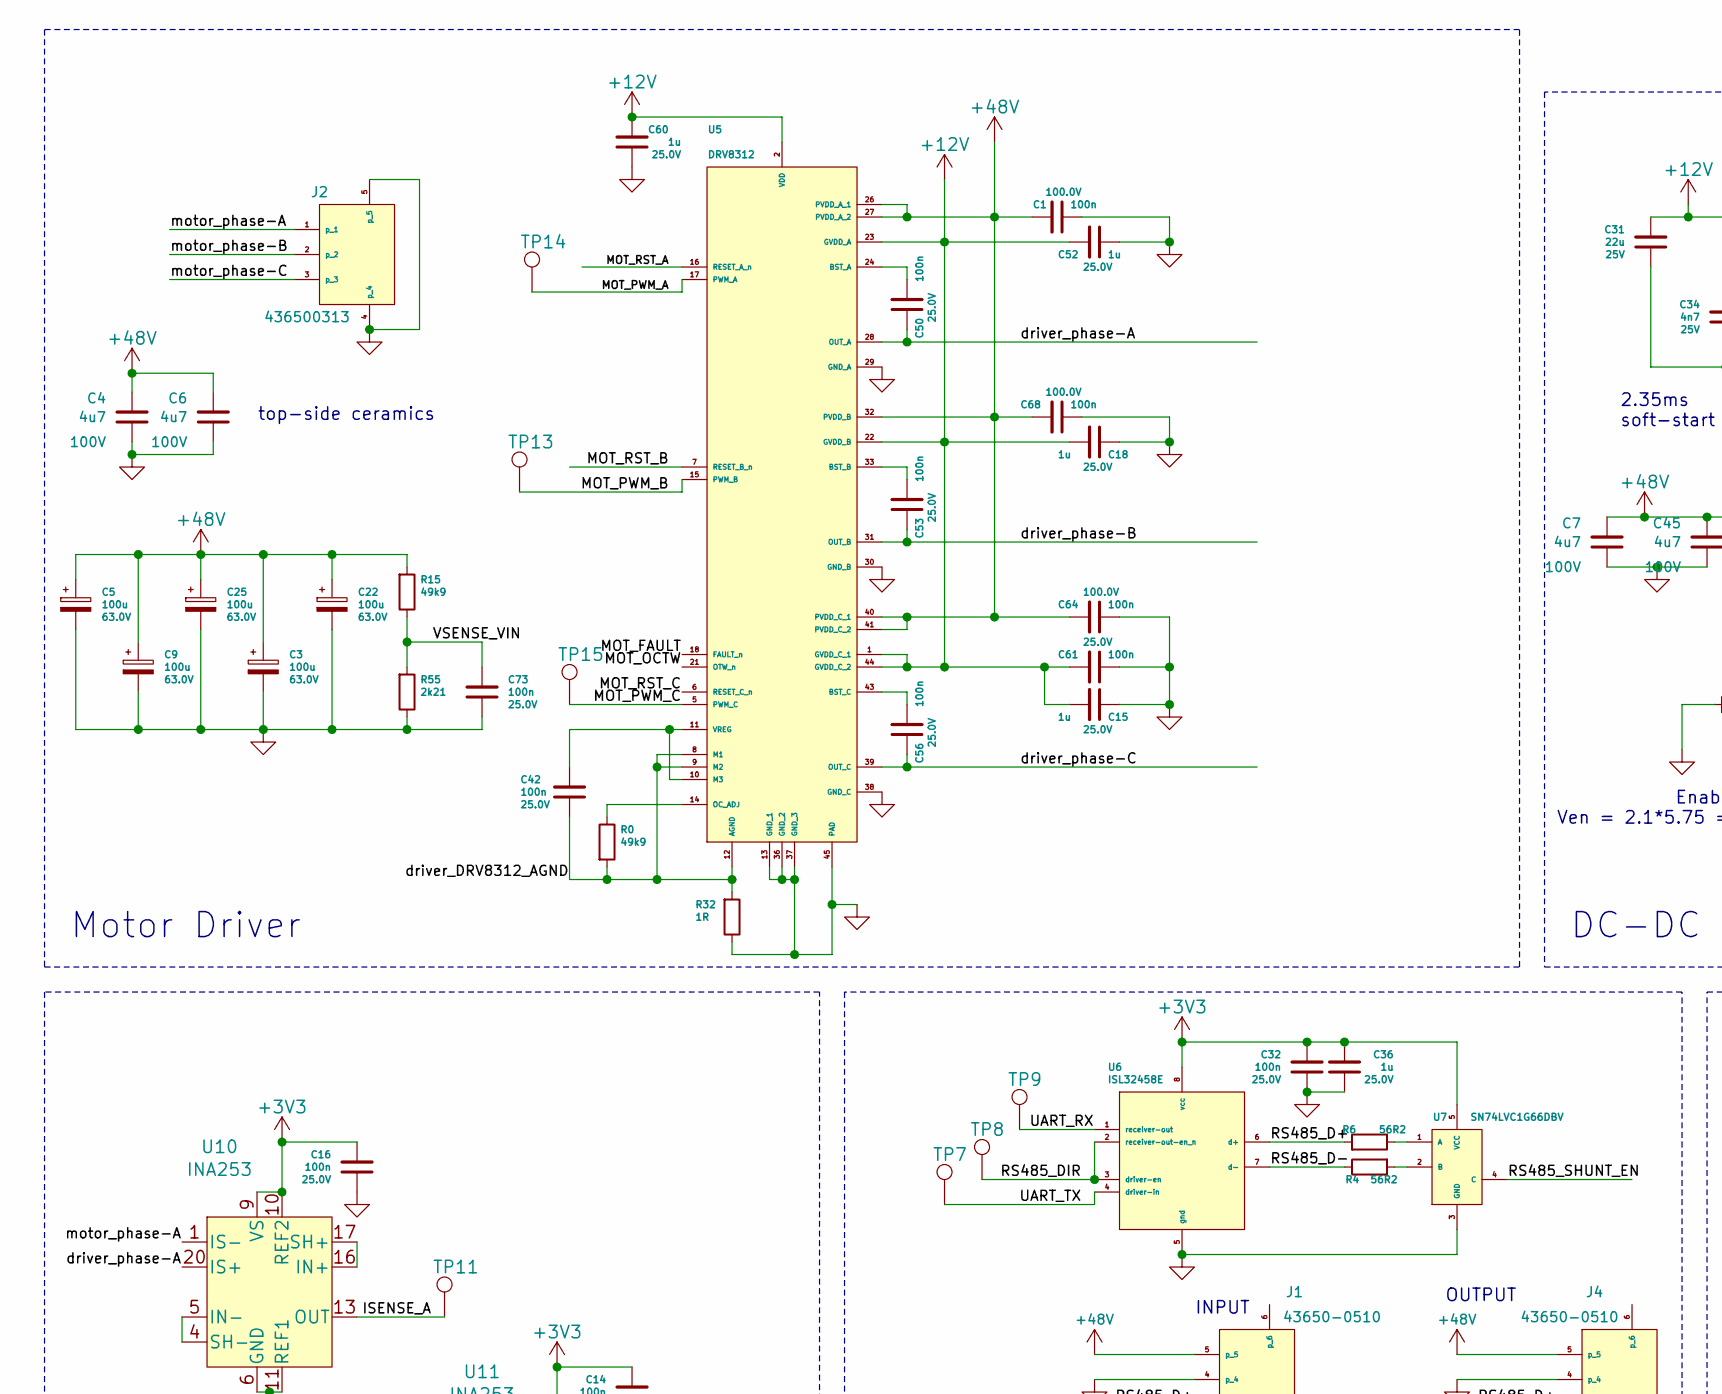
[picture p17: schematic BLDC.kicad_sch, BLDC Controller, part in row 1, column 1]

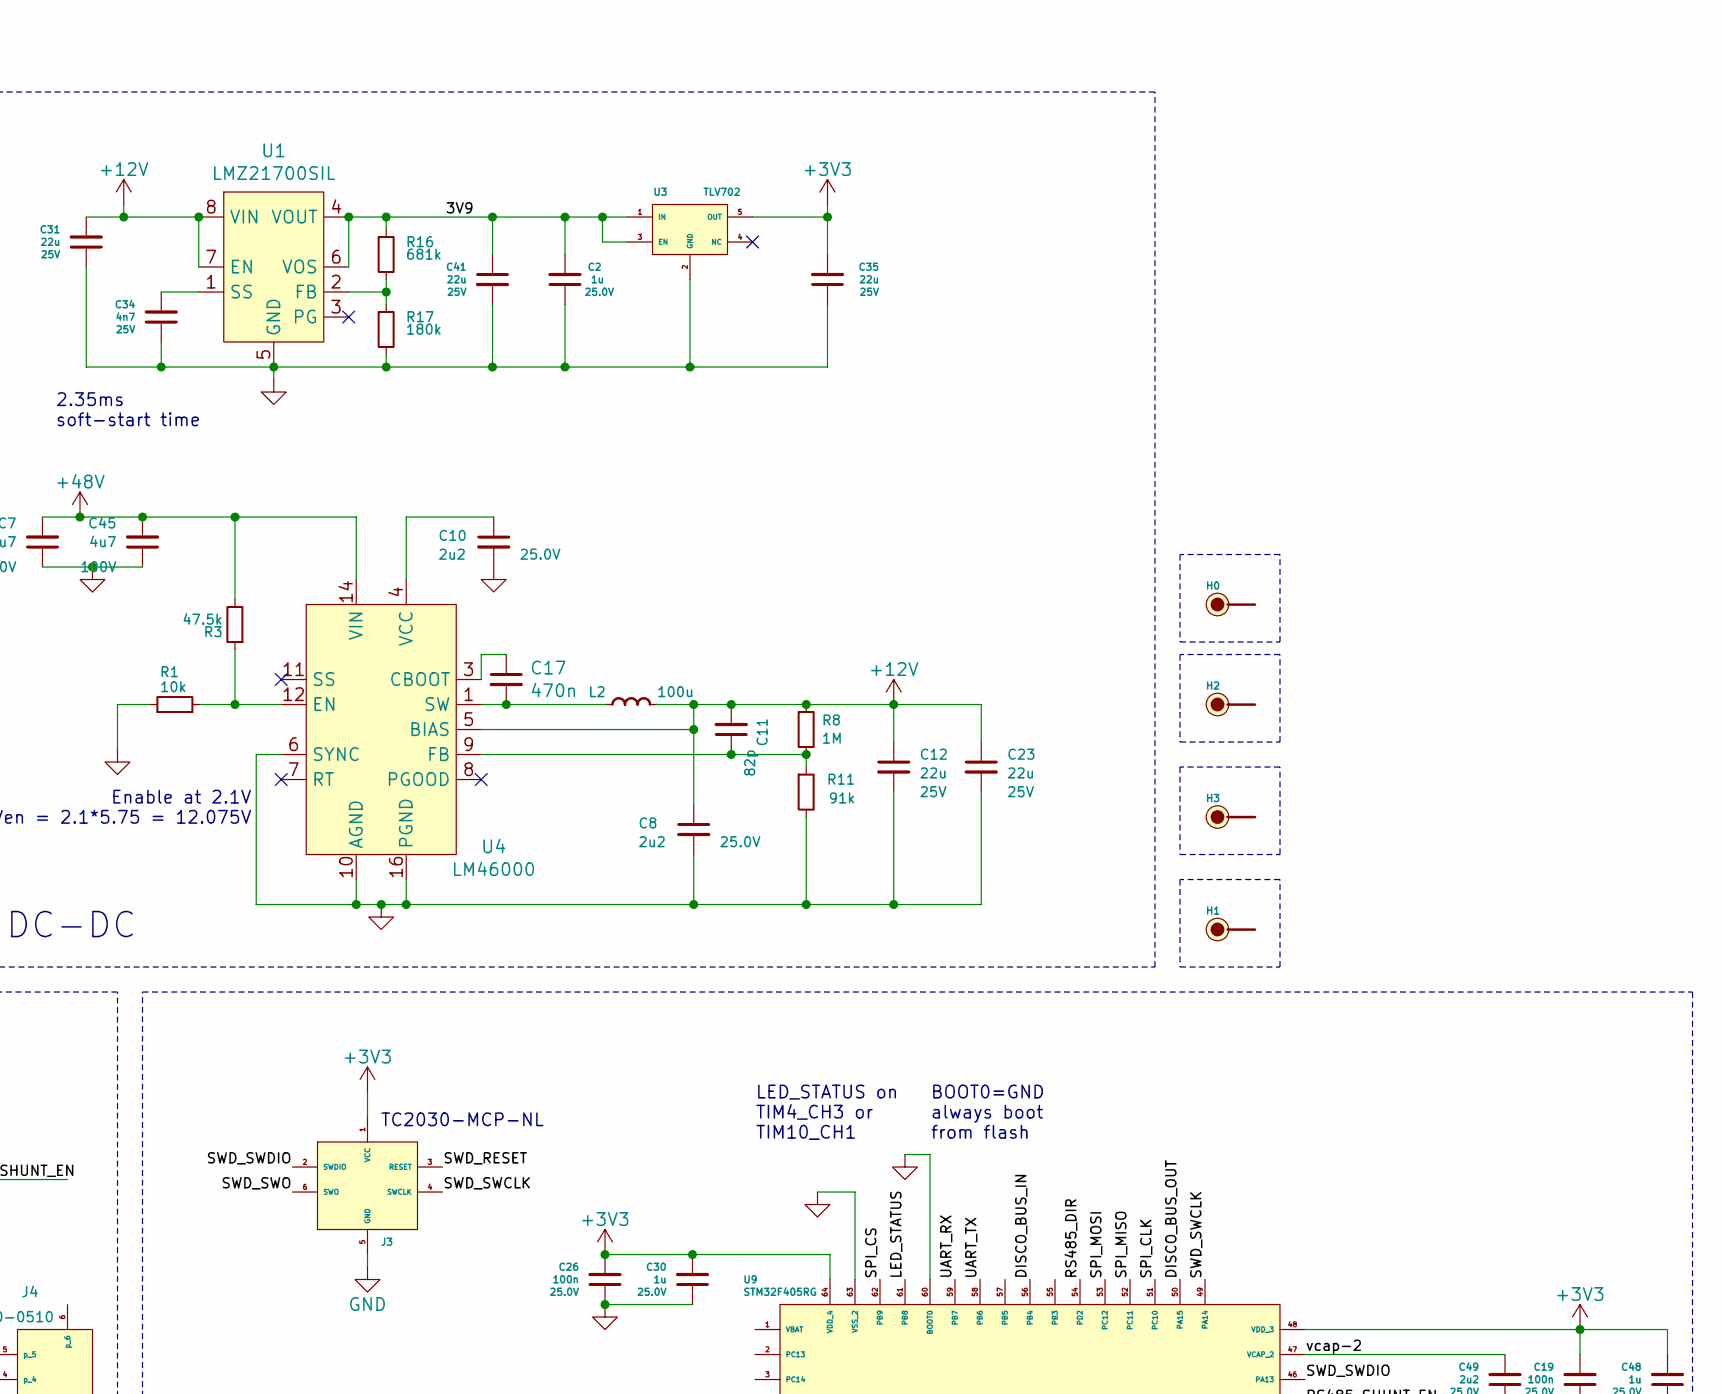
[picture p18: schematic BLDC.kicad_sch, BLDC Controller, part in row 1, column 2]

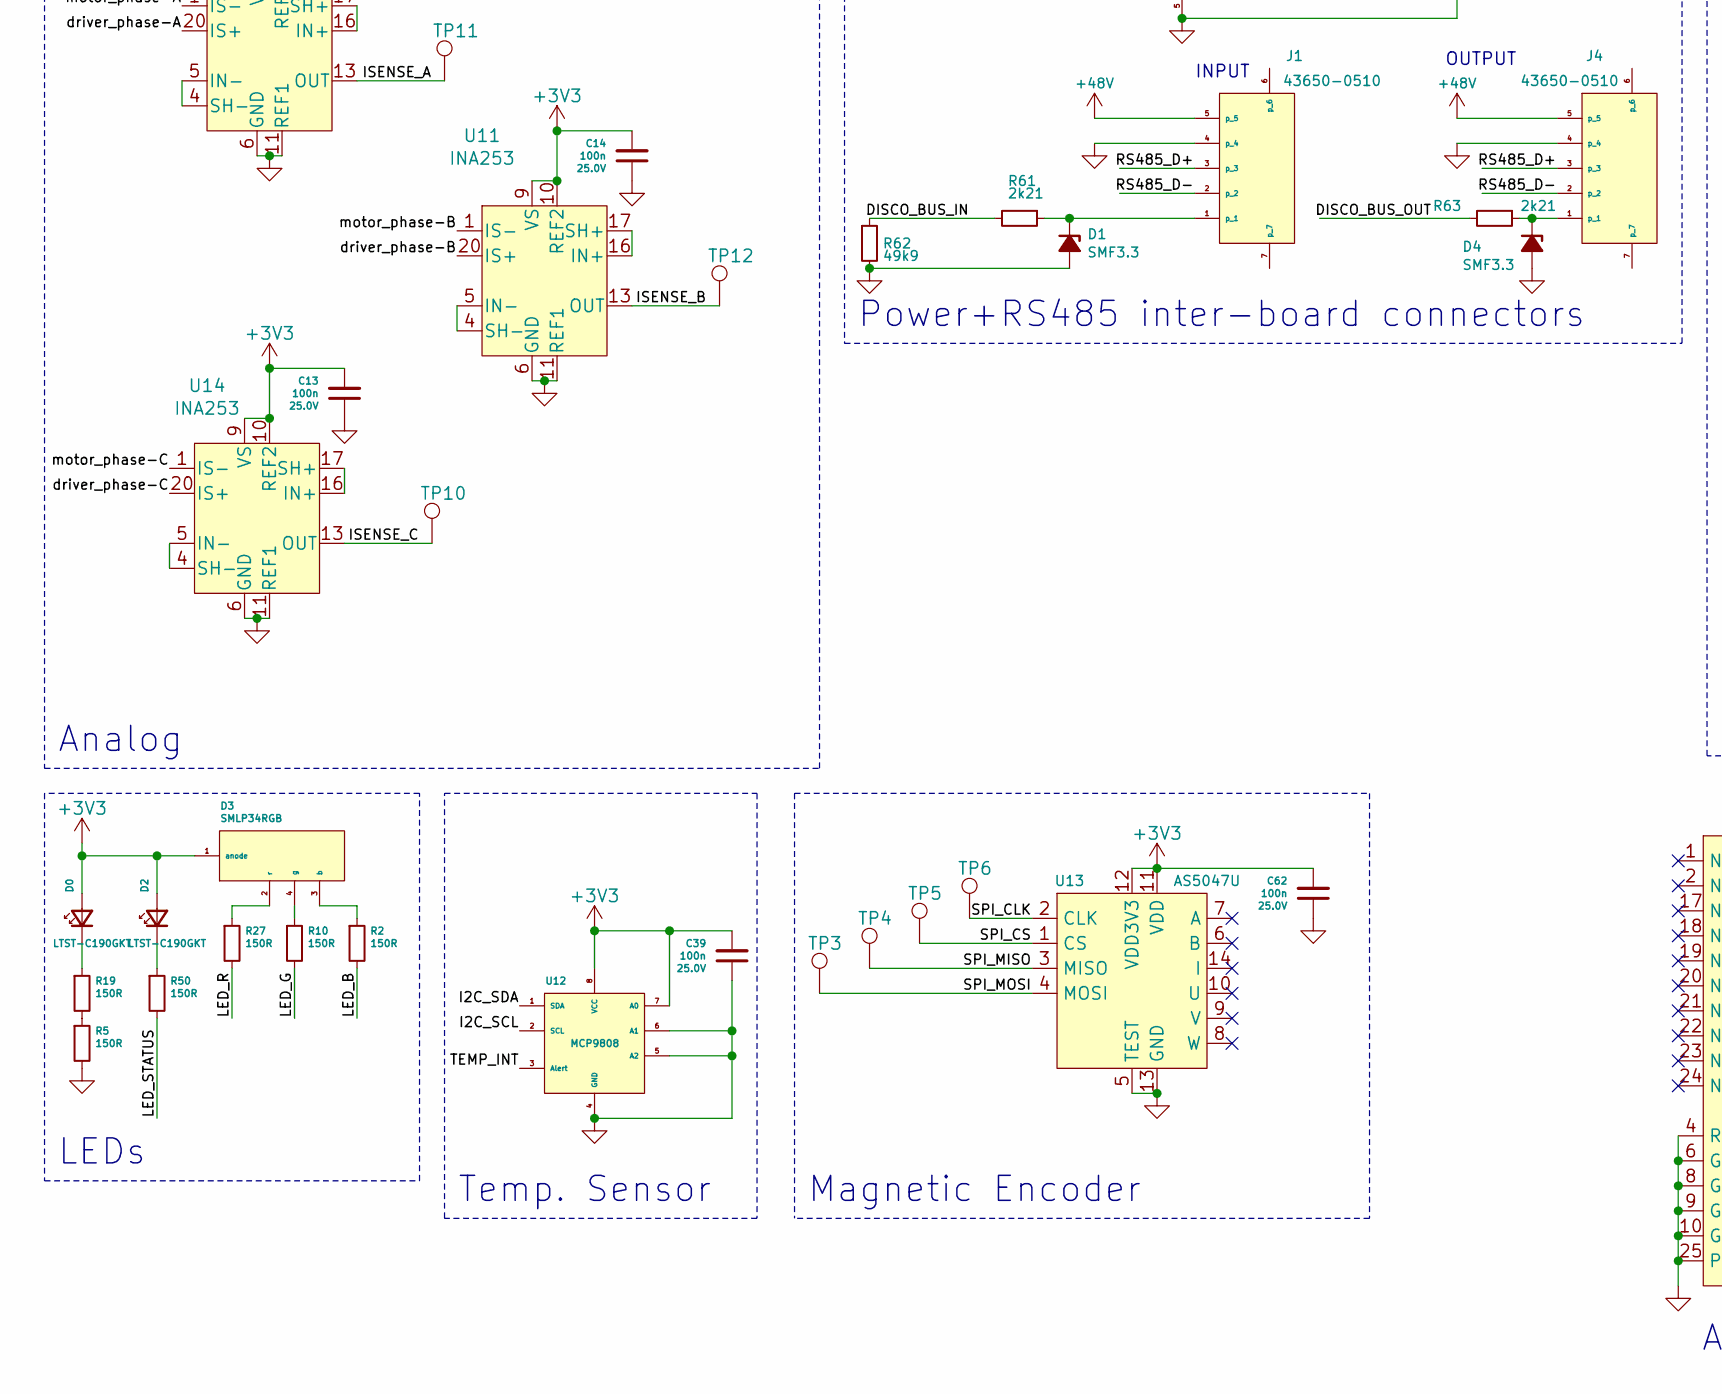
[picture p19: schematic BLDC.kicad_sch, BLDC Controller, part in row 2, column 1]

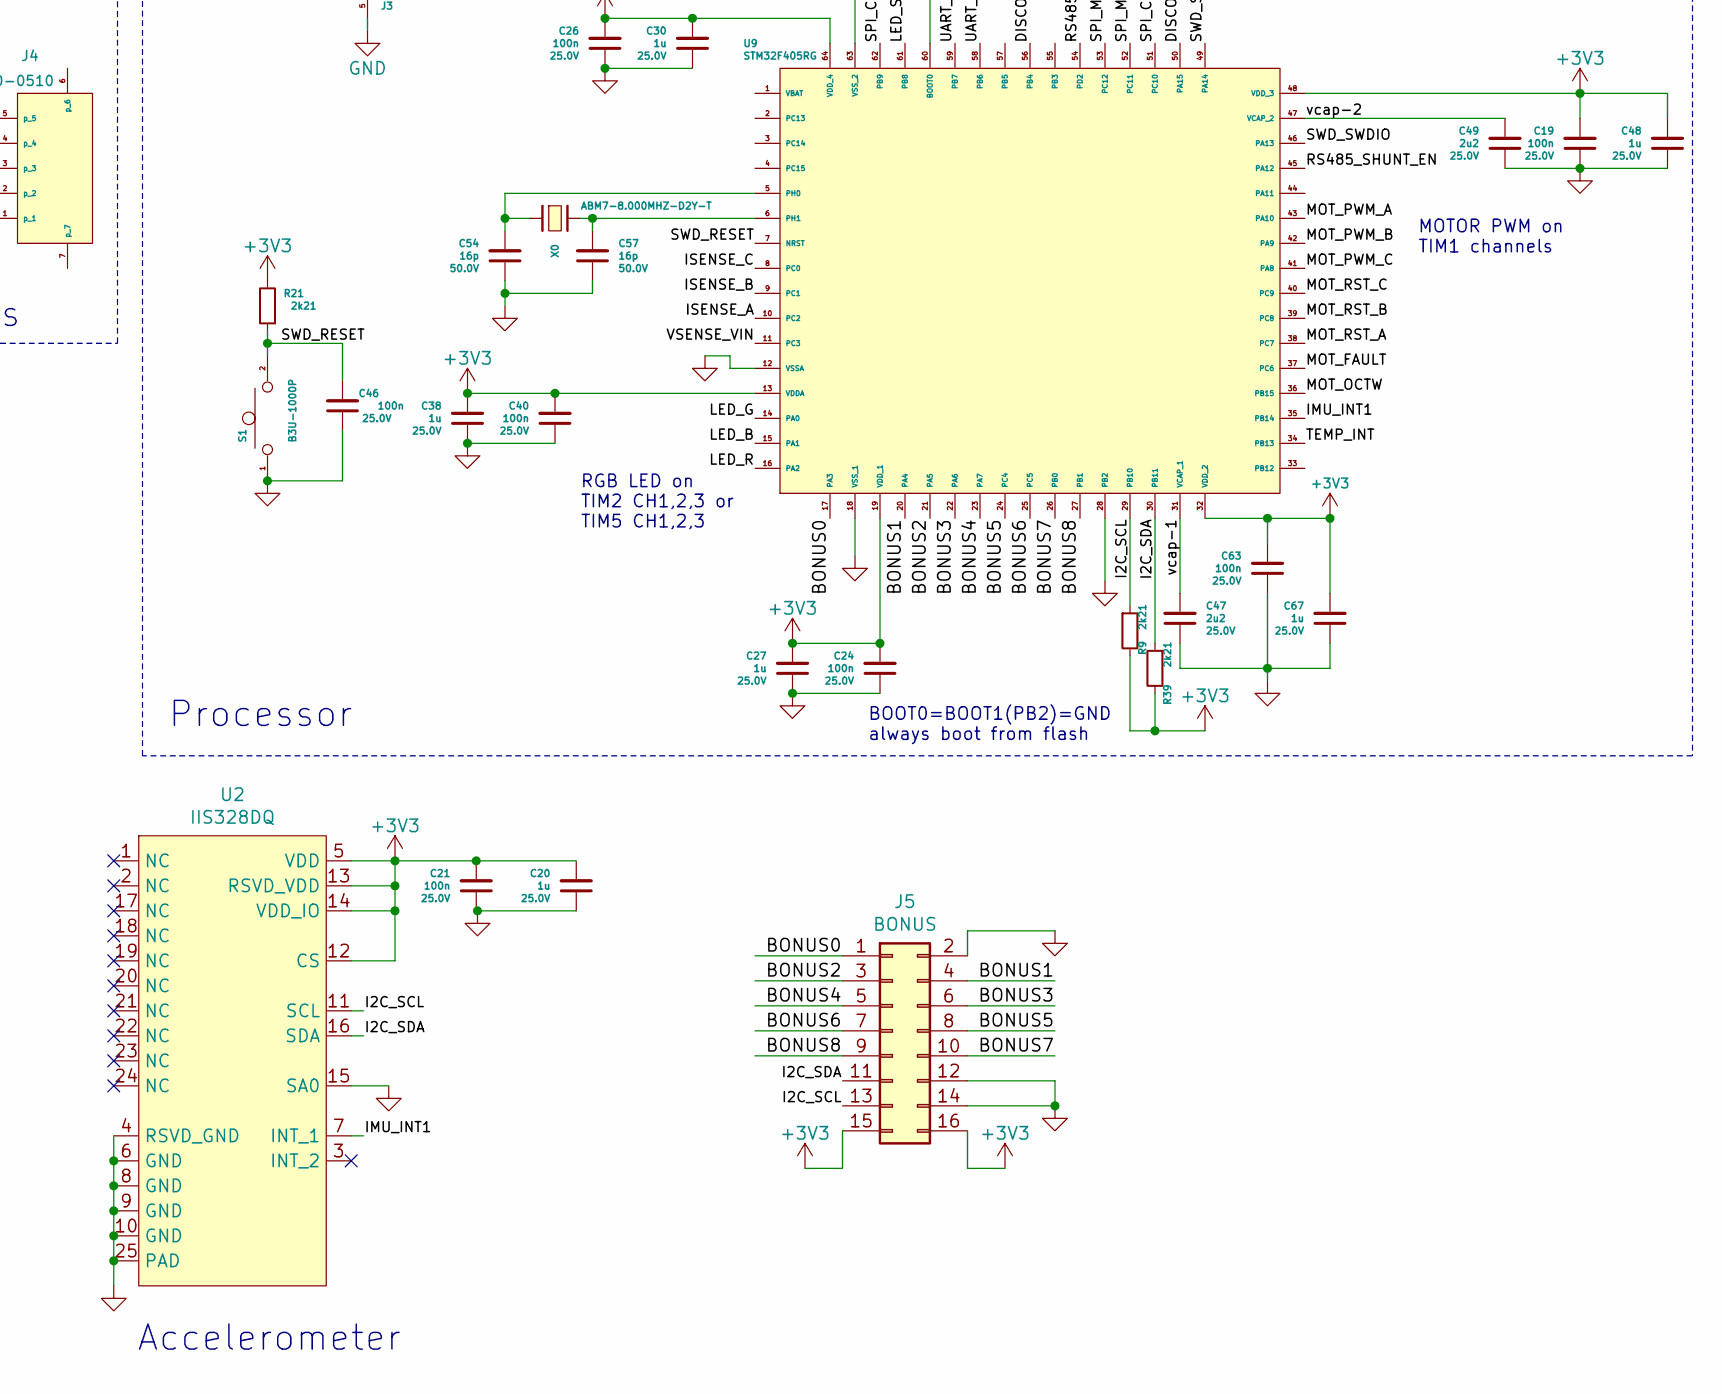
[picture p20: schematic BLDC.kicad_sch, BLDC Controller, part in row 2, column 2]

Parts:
C1, C64, C68: 100n; C_0603_1608Metric; Maximum Voltage 100.0V; Tolerance 10%; MPN CL10B104KC8NNNC
C2, C15, C18, C20, C27, C30, C36, C38, C48, C52, C60, C67: 1u; C_0402_1005Metric; Maximum Voltage 25.0V; Tolerance 10%; MPN GRM155R61E105KA12D
C3, C5, C9, C22, C25: 100u; CP_Elec_10x10; Maximum Voltage 63.0V; Tolerance 20%; MPN EEE-1JA101P
C4, C6, C7, C45: 4u7; C_1210_3225Metric; Maximum Voltage 100V; Tolerance 10%; MPN C3225X7S2A475K200AB
C8, C10, C47, C49: 2u2; C_0402_1005Metric; Maximum Voltage 25.0V; Tolerance 10%; MPN GRM155R61E225KE11D
C11: 82p; C_0402_1005Metric; Maximum Voltage 50V; Tolerance 10%; MPN 04025A820FAT2A
C12, C23, C31, C35, C41: 22u; C_1210_3225Metric; Maximum Voltage 25V; Tolerance 10%; MPN CL32A226KAJNNNE
C13, C14, C16, C19, C21, C24, C26, C32, C39, C40, C42, C46, C50, C53, C56, C61, C62, C63, C73: 100n; C_0402_1005Metric; Maximum Voltage 25.0V; Tolerance 10%; MPN CL05A104KA5NNNC
C17: 470n; C_0402_1005Metric; Maximum Voltage 10.0V; Tolerance 10%; MPN CL05A474KP5NNNC
C34: 4n7; C_0402_1005Metric; Maximum Voltage 25V; Tolerance 10%; MPN CC0402KRX7R8BB472
C54, C57: 16p; C_0402_1005Metric; Maximum Voltage 50.0V; Tolerance 5%; MPN GJM1555C1H160GB01D
D0, D2: LTST-C190GKT; D_0603_1608Metric; MPN LTST-C190GKT
D1, D4: SMF3.3; D_SOD-123F; MPN SMF3.3
D3: SMLP34RGB; rhom-SMLP34RGB-fp; MPN SMLP34RGB2W3
H0, H1, H2, H3: NONE; mounting-hole-pkg
J1, J4: 43650-0510; molex-436500511; MPN 436500510
J2: 436500313; molex-microfit-3-pkg; MPN 436500313
J3: DNP; TC2030-MCP-NL-pkg; MPN DNP
J5: BONUS; PinHeader_2x08_P2.54mm_Horizontal; MPN DNP
L2: 100u; L_7.3x7.3_H4.5; Tolerance 20%; MPN 744777920
R0, R15, R62: 49k9; R_0603_1608Metric; Tolerance 1%; MPN ERJ-3EKF4992V
R1: 10k; R_0402_1005Metric; Tolerance 1%; MPN AC0402FR-0710KL
R2, R5, R10, R19, R27, R50: 150R; R_0402_1005Metric; Tolerance 1%; MPN ERJ-2RKF1500X
R3: 47.5k; R_0402_1005Metric; Tolerance 1%; MPN RC0402FR-0747K5L
R4, R6: 56R2; R_0402_1005Metric; Tolerance 1%; MPN RC0402FR-0756R2L
R8: 1M; R_0402_1005Metric; Tolerance 1%; MPN RC0402FR-071ML
R9, R21, R39, R55, R61, R63: 2k21; R_0402_1005Metric; Tolerance 1%; MPN ERJ-2RKF2211X
R11: 91k; R_0402_1005Metric; Tolerance 1%; MPN RC0402FR-0791KL
R16: 681k; R_0402_1005Metric; Tolerance 1%; MPN RC0402FR-07681KL
R17: 180k; R_0402_1005Metric; Tolerance 1%; MPN RC0402FR-07180KL
R32: 1R; R_0805_2012Metric; Tolerance 1%; MPN ERJ-6DQF1R0V
S1: B3U-1000P; SW_B3U-1000P; MPN B3U-1000P
TP3, TP4, TP5, TP6, TP7, TP8, TP9, TP10, TP11, TP12, TP13, TP14, TP15: TestPoint; TestPoint_Pad_D1.0mm
U1: LMZ21700SIL; SIL0008E; MPN LMZ21700SILR
U2: IIS328DQ; QFN-24-1EP_4x4mm_P0.5mm_EP2.6x2.6mm; MPN IIS328DQTR
U3: TLV702; SOT-23-5; MPN TLV70233DBVR
U4: LM46000; PWP0016G; MPN LM46000PWPR
U5: DRV8312; HTSSOP-44; MPN DRV8312DDWR
U6: ISL32458E; SOIC-8_3.9x4.9mm_P1.27mm; MPN ISL32458EIBZ-T7A
U7: SN74LVC1G66DBV; SOT-23-5; MPN SN74LVC1G66DBV
U9: STM32F405RG; LQFP-64_10x10mm_P0.5mm; MPN STM32F405RGT6
U10, U11, U14: INA253; TSSOP-20_4.4x6.5mm_P0.65mm; MPN INA253A2IPW
U12: MCP9808; MSOP-8_3x3mm_P0.65mm; MPN MCP9808T-E/MS
U13: AS5047U; TSSOP-14_4.4x5mm_P0.65mm; MPN AS5047U-HTSM
X0: ABM7-8.000MHZ-D2Y-T; ABM7-8MHZ-D2Y-T-pkg; MPN ABM7-8.000MHZ-D2Y-T

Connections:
+3V3: C13.2, C14.2, C16.2, C19.2, C20.2, C21.2, C24.2, C26.2, C27.2, C30.2, C32.2, C35.2, C36.2, C38.2, C39.2, C40.2, C48.2, C62.2, C63.2, C67.2, D0.2 (A), D2.2 (A), D3.1 (anode), J3.1 (VCC), J5.15, J5.16, R9.2, R21.2, R39.2, U2.5 (VDD), U2.12 (CS), U2.13 (RSVD_VDD), U2.14 (VDD_IO), U3.5 (OUT), U6.8 (vcc), U7.5 (VCC), U9.13 (VDDA), U9.19 (VDD_1), U9.32 (VDD_2), U9.48 (VDD_3), U9.64 (VDD_4), U10.9 (VS), U10.10 (REF2), U11.9 (VS), U11.10 (REF2), U12.7 (A0), U12.8 (VCC), U13.11 (VDD), U13.12 (VDD3V3), U14.9 (VS), U14.10 (REF2)
+12V: C8.1, C11.2, C12.1, C15.2, C18.2, C23.1, C31.2, C52.2, C60.2, C61.2, L2.2 (p), R8.1, U1.7 (EN), U1.8 (VIN), U4.5 (BIAS), U5.1 (GVDD_C_1), U5.2 (VDD), U5.22 (GVDD_B), U5.23 (GVDD_A), U5.44 (GVDD_C_2)
+48V: C1.2, C3.1, C4.2, C5.1, C6.2, C7.2, C9.1, C22.1, C25.1, C45.2, C64.2, C68.2, J1.5 (p), J4.5 (p), R3.2, R15.1, U4.13 (VIN), U4.14 (VIN), U5.26 (PVDD_A_1), U5.27 (PVDD_A_2), U5.32 (PVDD_B), U5.40 (PVDD_C_1), U5.41 (PVDD_C_2)
/3V9: C2.2, C41.1, R16.1, U1.4 (VOUT), U1.6 (VOS), U3.1 (IN), U3.3 (EN)
/BONUS0: J5.1, U9.17 (PA3)
/BONUS1: J5.4, U9.20 (PA4)
/BONUS2: J5.3, U9.21 (PA5)
/BONUS3: J5.6, U9.22 (PA6)
/BONUS4: J5.5, U9.23 (PA7)
/BONUS5: J5.8, U9.24 (PC4)
/BONUS6: J5.7, U9.25 (PC5)
/BONUS7: J5.10, U9.26 (PB0)
/BONUS8: J5.9, U9.27 (PB1)
/DISCO_BUS_IN: R61.2, R62.1, U9.56 (PB4)
/DISCO_BUS_OUT: R63.2, U9.50 (PA15)
/I2C_SCL: J5.13, R9.1, U2.11 (SCL), U9.29 (PB10), U12.2 (SCL)
/I2C_SDA: J5.11, R39.1, U2.16 (SDA), U9.30 (PB11), U12.1 (SDA)
/IMU_INT1: U2.7 (INT_1), U9.35 (PB14)
/ISENSE_A: TP11.1, U9.10 (PC2), U10.13 (OUT)
/ISENSE_B: TP12.1, U9.9 (PC1), U11.13 (OUT)
/ISENSE_C: TP10.1, U9.8 (PC0), U14.13 (OUT)
/LED_B: R2.2, U9.15 (PA1)
/LED_G: R10.2, U9.14 (PA0)
/LED_R: R27.2, U9.16 (PA2)
/LED_STATUS: R50.2, U9.61 (PB8)
/MOT_FAULT: U5.18 (FAULT_n), U9.37 (PC6)
/MOT_OCTW: U5.21 (OTW_n), U9.36 (PB15)
/MOT_PWM_A: TP14.1, U5.17 (PWM_A), U9.43 (PA10)
/MOT_PWM_B: TP13.1, U5.15 (PWM_B), U9.42 (PA9)
/MOT_PWM_C: TP15.1, U5.5 (PWM_C), U9.41 (PA8)
/MOT_RST_A: U5.16 (RESET_A_n), U9.38 (PC7)
/MOT_RST_B: U5.7 (RESET_B_n), U9.39 (PC8)
/MOT_RST_C: U5.6 (RESET_C_n), U9.40 (PC9)
/RS485_D+: J1.3 (p), J4.3 (p), R6.1, U6.6 (d+)
/RS485_D-: J1.2 (p), J4.2 (p), R4.2, U6.7 (d-)
/RS485_DIR: TP8.1, U6.2 (receiver-out-en_n), U6.3 (driver-en), U9.54 (PD2)
/RS485_SHUNT_EN: U7.4 (C), U9.45 (PA12)
/SPI_CLK: TP6.1, U9.51 (PC10), U13.2 (CLK)
/SPI_CS: TP5.1, U9.62 (PB9), U13.1 (CS)
/SPI_MISO: TP4.1, U9.52 (PC11), U13.3 (MISO)
/SPI_MOSI: TP3.1, U9.53 (PC12), U13.4 (MOSI)
/SWD_RESET: C46.2, J3.3 (RESET), R21.1, S1.2, U9.7 (NRST)
/SWD_SWCLK: J3.4 (SWCLK), U9.49 (PA14)
/SWD_SWDIO: J3.2 (SWDIO), U9.46 (PA13)
/SWD_SWO: J3.6 (SWO)
/TEMP_INT: U9.34 (PB13), U12.3 (Alert)
/UART_RX: TP9.1, U6.1 (receiver-out), U9.59 (PB7)
/UART_TX: TP7.1, U6.4 (driver-in), U9.58 (PB6)
/VSENSE_VIN: C73.2, R15.2, R55.1, U9.11 (PC3)
/driver_DRV8312_AGND: C42.1, R0.1, R32.1, U5.8 (M1), U5.9 (M2), U5.12 (AGND)
/driver_phase-A: C50.1, U5.28 (OUT_A), U10.18 (IS+), U10.19 (IS+), U10.20 (IS+)
/driver_phase-B: C53.1, U5.31 (OUT_B), U11.18 (IS+), U11.19 (IS+), U11.20 (IS+)
/driver_phase-C: C56.1, U5.39 (OUT_C), U14.18 (IS+), U14.19 (IS+), U14.20 (IS+)
/motor_phase-A: J2.1 (p), U10.1 (IS-), U10.2 (IS-), U10.3 (IS-)
/motor_phase-B: J2.2 (p), U11.1 (IS-), U11.2 (IS-), U11.3 (IS-)
/motor_phase-C: J2.3 (p), U14.1 (IS-), U14.2 (IS-), U14.3 (IS-)
/vcap-1: C47.2, U9.31 (VCAP_1)
/vcap-2: C49.2, U9.47 (VCAP_2)
GND: C1.1, C2.1, C3.2, C4.1, C5.2, C6.1, C7.1, C8.2, C9.2, C10.2, C12.2, C13.1, C14.1, C15.1, C16.1, C18.1, C19.1, C20.1, C21.1, C22.2, C23.2, C24.1, C25.2, C26.1, C27.1, C30.1, C31.1, C32.1, C34.1, C35.1, C36.1, C38.1, C39.1, C40.1, C41.2, C45.1, C46.1, C47.1, C48.1, C49.1, C52.1, C54.1, C57.1, C60.1, C61.1, C62.1, C63.1, C64.1, C67.1, C68.1, C73.1, D1.2 (A), D4.2 (A), J1.4 (p), J2.4 (p), J2.5 (p), J3.5 (GND), J4.4 (p), J5.2, J5.12, J5.14, R1.1, R5.2, R11.2, R17.2, R32.2, R55.2, R62.2, S1.1, U1.5 (GND), U1.9 (PAD), U2.4 (RSVD_GND), U2.6 (GND), U2.8 (GND), U2.9 (GND), U2.10 (GND), U2.15 (SA0), U2.25 (PAD), U3.2 (GND), U4.6 (SYNC), U4.10 (AGND), U4.15 (PGND), U4.16 (PGND), U4.17 (AGND), U5.13 (GND_1), U5.29 (GND_A), U5.30 (GND_B), U5.36 (GND_2), U5.37 (GND_3), U5.38 (GND_C), U5.45 (PAD), U6.5 (gnd), U7.3 (GND), U9.12 (VSSA), U9.18 (VSS_1), U9.28 (PB2), U9.60 (BOOT0), U9.63 (VSS_2), U10.6 (GND), U10.11 (REF1), U10.15 (RES), U11.6 (GND), U11.11 (REF1), U11.15 (RES), U12.4 (GND), U12.5 (A2), U12.6 (A1), U13.5 (TEST), U13.13 (GND), U14.6 (GND), U14.11 (REF1), U14.15 (RES)
unnamed: C10.1, U4.4 (VCC)
unnamed: C11.1, R8.2, R11.1, U4.9 (FB)
unnamed: C17.1, U4.3 (CBOOT)
unnamed: C17.2, L2.1 (p), U4.1 (SW), U4.2 (SW)
unnamed: C34.2, U1.1 (SS)
unnamed: C42.2, U5.10 (M3), U5.11 (VREG)
unnamed: C50.2, U5.24 (BST_A)
unnamed: C53.2, U5.33 (BST_B)
unnamed: C54.2, U9.5 (PH0), X0.1 (p)
unnamed: C56.2, U5.43 (BST_C)
unnamed: C57.2, U9.6 (PH1), X0.2 (p)
unnamed: D0.1 (K), R19.1
unnamed: D1.1 (K), J1.1 (p), R61.1
unnamed: D2.1 (K), R50.1
unnamed: D3.2 (r), R27.1
unnamed: D3.3 (b), R2.1
unnamed: D3.4 (g), R10.1
unnamed: D4.1 (K), J4.1 (p), R63.1
unnamed: R0.2, U5.14 (OC_ADJ)
unnamed: R1.2, R3.1, U4.12 (EN)
unnamed: R4.1, U7.2 (B)
unnamed: R6.2, U7.1 (A)
unnamed: R16.2, R17.1, U1.2 (FB)
unnamed: R5.1, R19.2
unnamed: U10.4 (SH-), U10.5 (IN-)
unnamed: U10.16 (IN+), U10.17 (SH+)
unnamed: U11.4 (SH-), U11.5 (IN-)
unnamed: U11.16 (IN+), U11.17 (SH+)
unnamed: U14.4 (SH-), U14.5 (IN-)
unnamed: U14.16 (IN+), U14.17 (SH+)

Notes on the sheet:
Analog
Motor Driver
Magnetic Encoder
TC2030-MCP-NL
Temp. Sensor
MOTOR PWM on TIM1 channels
RGB LED on TIM2 CH1,2,3 or TIM5 CH1,2,3
2.35ms soft-start time
LED_STATUS on TIM4_CH3 or TIM10_CH1
Accelerometer
BOOT0=GND always boot from flash
INPUT
DC-DC
LEDs
BOOT0=BOOT1(PB2)=GND always boot from flash
Enable at 2.1V Ven = 2.1*5.75 = 12.075V
Power+RS485 inter-board connectors
OUTPUT
top-side ceramics
Processor

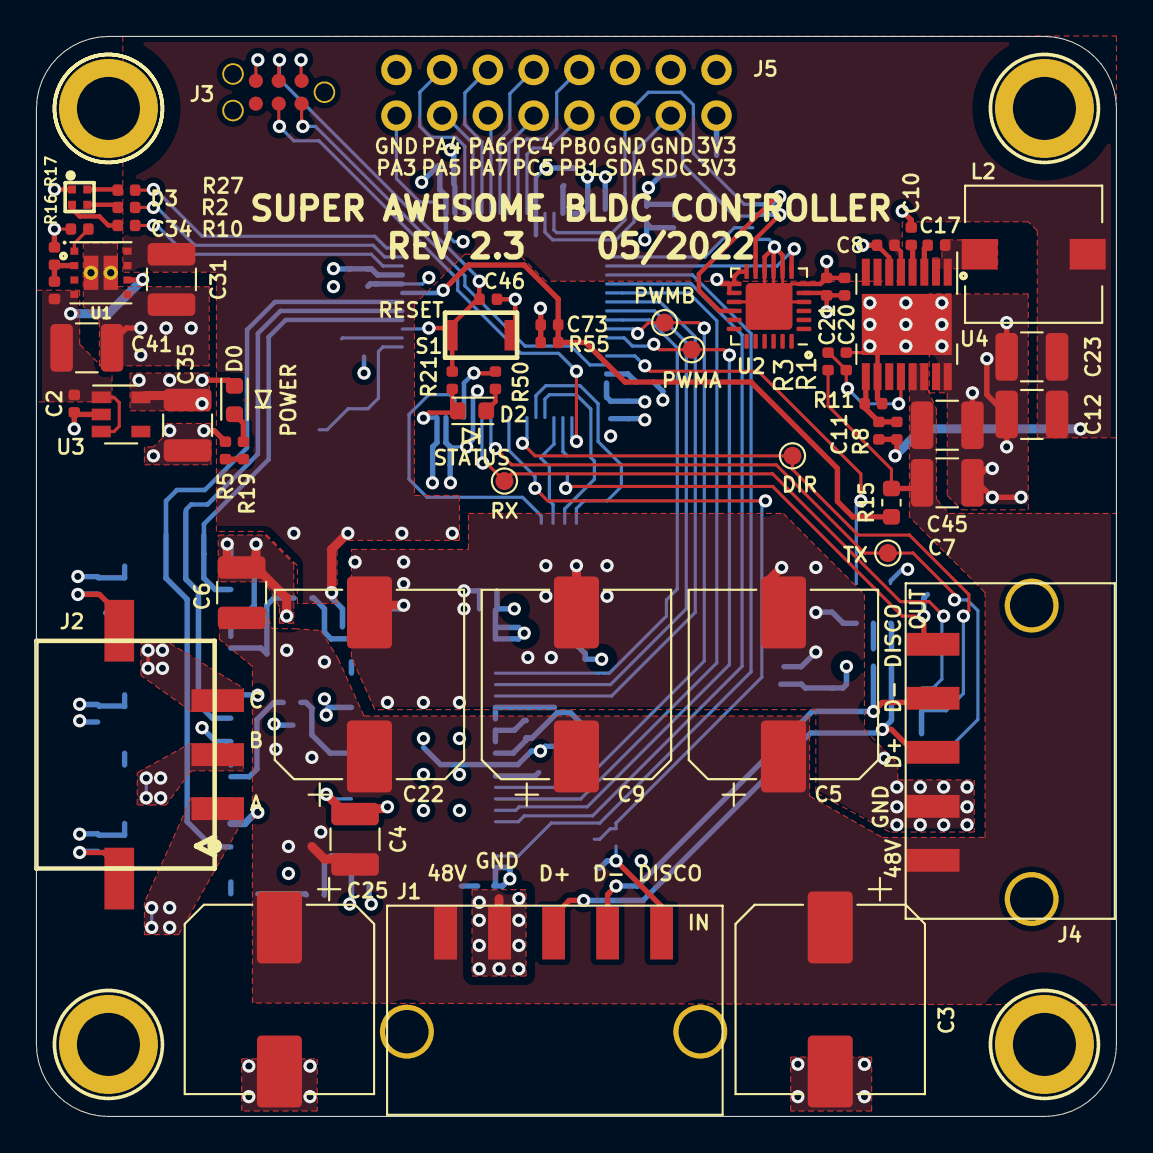
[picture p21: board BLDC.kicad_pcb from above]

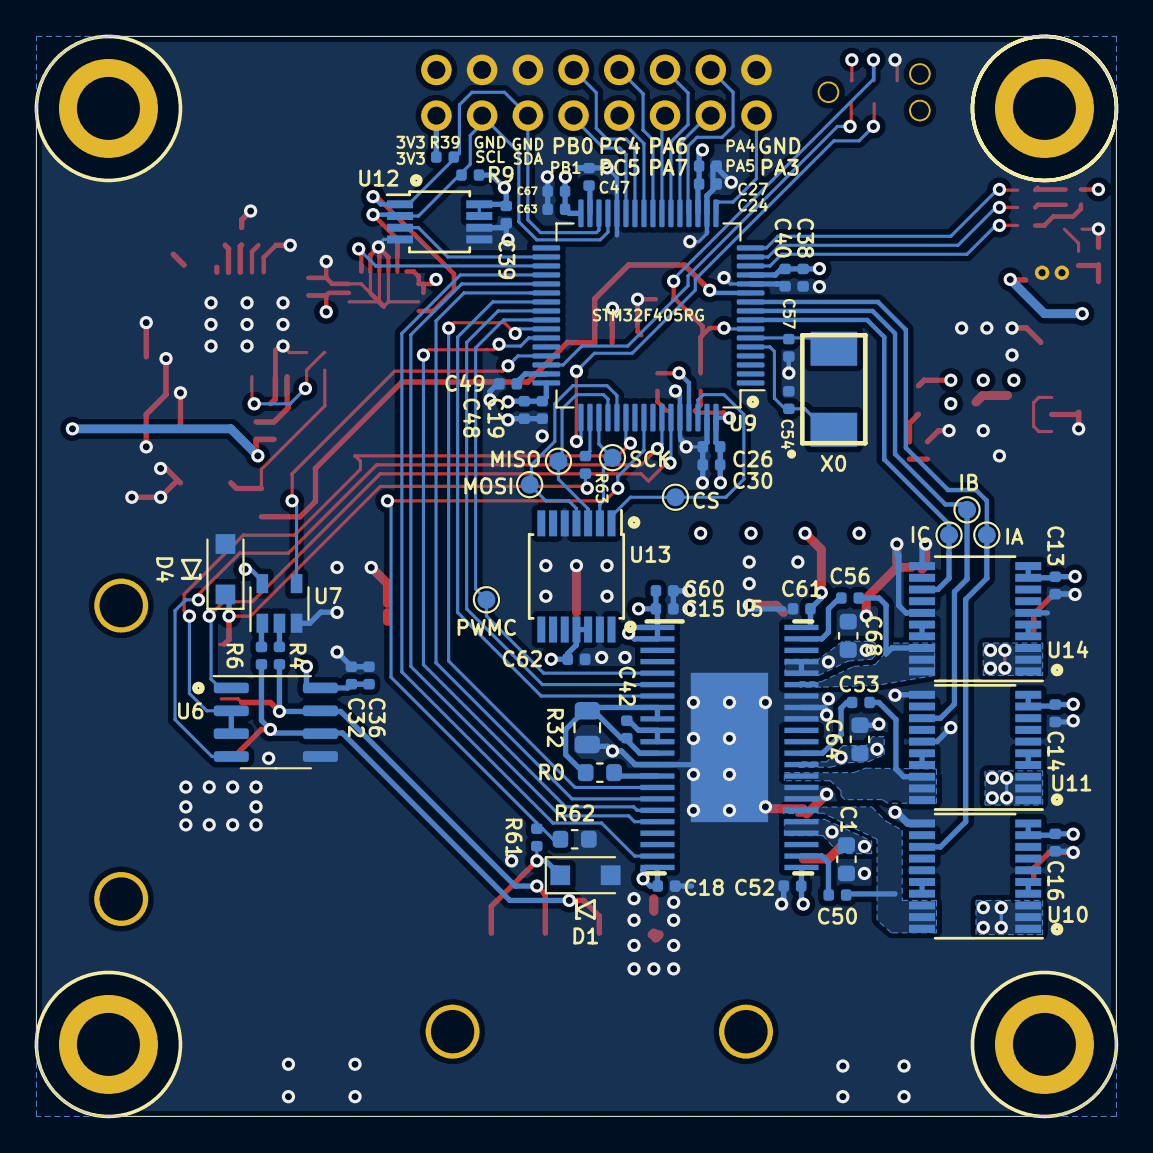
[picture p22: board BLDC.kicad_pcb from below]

Board: 4 copper layers, 60.0 x 60.0 mm, 124 parts (62 on the bottom side), 88 nets.

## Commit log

2019-07-05 Blue V2 hardware merge
    [BLDC.kicad_pcb, BLDC.sch, bldc-controller.kicad_pcb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]
2019-07-29 First draft of rework, major changes to placement, routing and components choice
    [BLDC.kicad_pcb, BLDC.sch]
2019-07-31 Breaking changes, changed IO pin assigment of STM32 to simplify routing, various optimizations
    [BLDC.kicad_pcb, BLDC.sch]
2019-08-05 Cleared DRC errors, changed minimum track width to 6 mil for cheaper manufacturing.
    [BLDC.kicad_pcb, BLDC.sch]
2019-08-06 Removed capacitor that would be in contact in 3d mounting, fixed silkscreen
    [BLDC.kicad_pcb, BLDC.sch]
2019-08-08 WIP changed capacitors back to SMT
    [BLDC.kicad_pcb, BLDC.sch]
2019-08-08 Fixed DRC errors, added ground pour, fixed courtyards of connectors and DRV chip to allow more packed designs
    [BLDC.kicad_pcb, BLDC.sch]
2019-08-08 Added ground pour in bottom layer for thermal dissipation and current return
    [BLDC.kicad_pcb, BLDC.sch]
2019-08-08 add a bit more clearance to 48v pour
    [BLDC.kicad_pcb]
2019-08-09 Added 3d models for molex connectors
    [436500313.stp, 436500513.stp, BLDC.kicad_pcb]
2019-08-09 Changed J1 connector to through hole and moved to middle of PCB
    [436500511.stp, BLDC.kicad_pcb, BLDC.sch]
2019-08-09 WIP, adding 3d models, choosing kicad official footprints. TODO fix possible conflict between capacitor and accelerometer / temperature sensor
    [BLDC.kicad_pcb]
2019-08-09 Expanded 48V pour, arranged components to reduce risk of collision with capacitors
    [BLDC.kicad_pcb]
2019-08-09 Fixed inductor footprints and added 3d models
    [BLDC.kicad_pcb, clf6045.step, clf7045.step]
2019-08-09 Added 3d models for remaining parts
    [ABM7.STEP, B3U_1000P.step, BLDC.kicad_pcb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]
2019-08-09 toying with some major layout changes to move the MCU far away from EMI
    [BLDC.kicad_pcb, BLDC.sch]
2019-08-09 Moving capacitors slightly
    [BLDC.kicad_pcb]
2019-08-10 Preliminary routing of new STM position, still to check and refine
    [BLDC.kicad_pcb, BLDC.sch]
2019-08-10 WIP adding output snubbers and trying to improve high-power paths
    [BLDC.kicad_pcb, BLDC.sch]
2019-08-11 finish draft of high-power net routes. clean up throughout.
    [BLDC.kicad_pcb, BLDC.sch]
2019-08-12 minimize rs485 stubs. more power net cleanup. bigger vias.
    [BLDC.kicad_pcb]
2019-08-13 massively increase size of ground bus on middle of top layer. use big vias.
    [BLDC.kicad_pcb]
2019-08-14 route cleanup and enlarge vias
    [BLDC.kicad_pcb]
2019-08-14 WIP simplify power supply designs
    [BLDC.kicad_pcb, BLDC.sch]
2019-08-16 Finished simplified power rail design
    [BLDC.kicad_pcb, BLDC.sch, LM5163.stp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]
2019-08-19 switch to larger accel package. enlarge all vias and traces. clean up.
    [BLDC.kicad_pcb, BLDC.sch]
2019-08-19 Adding In/Out labels to Molex Connectors
    [BLDC.kicad_pcb]
2019-08-20 use NRST for SWD_RESET
    [BLDC.kicad_pcb, BLDC.sch]
2019-08-20 add 1v2 reference to INA250 and MCU ADC
    [BLDC.kicad_pcb, BLDC.sch]
2019-08-21 Added BOM
    [BLDC.kicad_pcb, BLDC.sch]
2019-08-22 Added part number and updated capacitance for bulk caps
    [BLDC.sch]
2019-08-22 add title and current rev of bom generator script
    [BLDC.sch]
2019-08-22 nicer warnings for safetly-ignored schematic entries
2019-08-22 Added consolidated BoM generated and KiBoM submodule used to generate it
    [BLDC.sch, BLDC_bom_A.csv]
2019-08-23 consolidate lots of BOM line items, lots of clean up
    [BLDC.kicad_pcb, BLDC.sch]
2019-08-23 fix part numbers, move programming connector, add i2c test points
    [BLDC.kicad_pcb, BLDC.sch, BLDC_bom_A.csv]
2019-08-23 add test points to SPI bus
    [BLDC.kicad_pcb, BLDC.sch]
2019-08-23 more test points
    [BLDC.kicad_pcb, BLDC.sch]
2019-08-23 PWM test points
    [BLDC.kicad_pcb, BLDC.sch]
2019-08-23 add TVS diodes to input and output disco bus connector pins
    [BLDC.kicad_pcb, BLDC.sch]
2019-08-24 clear out north edge of PCB for upcoming bonus header
    [BLDC.kicad_pcb, BLDC.sch]
2019-08-24 WIP adding bonus header to north edge
    [BLDC.kicad_pcb, BLDC.sch]
2019-08-25 finish up bonus connector
    [BLDC.kicad_pcb, BLDC.sch]
2019-08-25 a bit more pcb cleanup, add slow-start cap MPN and gerbv project
    [BLDC.kicad_pcb, BLDC.sch]
2019-08-25 update BOM file
    [BLDC.sch, BLDC_bom_A.csv]
2019-08-26 Aesthetic, add LMZ regulator 3d model
    [BLDC.kicad_pcb, LMZ21701.stp]
2019-08-26 a bit of trivial cleanup. sent out for quote
    [BLDC.kicad_pcb]
2019-10-04 WIP new revision, change INA250 to INA253 (higher bandwidth), regulator to low EMI version
    [BLDC.kicad_pcb, BLDC.sch]
2019-10-05 tinker with layout, mostly with 12v dc-dc
    [BLDC.kicad_pcb, BLDC.sch]
2019-10-07 Added 3d model for regulator, routed all design (passing DRC)
    [BLDC.kicad_pcb, BLDC.sch, PWP0016G.stp]
2019-10-08 place/route tweaks. move accelerometer to top layer.
    [BLDC.kicad_pcb, BLDC.sch]
2019-10-09 Routed I2C, updated BOM
    [BLDC.kicad_pcb, BLDC.sch, BLDC_bom_A.csv]
2019-10-09 Cosmetic improvements to silkscreen
    [BLDC.kicad_pcb]
2019-10-09 Updated 3d models to include latest inductor
    [BLDC.kicad_pcb, STEP-WE-PD-7345-Plastic-rev1.stp]
2019-10-14 add another via for each motor-phase trace, and more silkscreen markings
    [BLDC.kicad_pcb, BLDC.sch]
2019-10-14 switch 4u7 to in-stock TDK part number
    [BLDC.sch, BLDC_bom_A.csv]
2019-10-14 export fabrication files for v2.2
    [BLDC.kicad_pcb]
2019-12-10 Added 3d models and library for molex connectors
    [022053031.stp, 436500213.stp]
2019-12-10 Added nanofit connector 3d model
    [1053131202.stp]
2019-12-31 Fixed I2C address of temperature sensor
    TODO regenerate gerber files
    [BLDC.kicad_pcb, BLDC.sch]
2020-09-13 Adjusted LM46000 to start-up at gt 12V instead of Vmin (#8)
    * Adjusted LM46000 to start up at gt 12V instead of Vmin
    * Correcting voltage divider
    [BLDC.kicad_pcb, BLDC.kicad_sch, BLDC.sch]
2022-09-23 Kicad6 (#13)
    * Upgrade to kicad6
    * Fix DRC checks
    [BLDC.kicad_pcb, BLDC.kicad_sch]
